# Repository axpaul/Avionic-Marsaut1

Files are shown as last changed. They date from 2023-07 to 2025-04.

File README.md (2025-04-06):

# Avionic-Marsaut1
       
## Marsaut_1 est une fusée expérimentale équipée d'une avionique (électronique de bord) créée par Mines Space. La version n°2 a été lancée au C'space 2022.

> *© 2022 Paul Miailhe, all rights reserved.*  
> *Material licensed under [→ CC BY-NC-SA 4.0](https://creativecommons.org/licenses/by-nc-sa/4.0)*

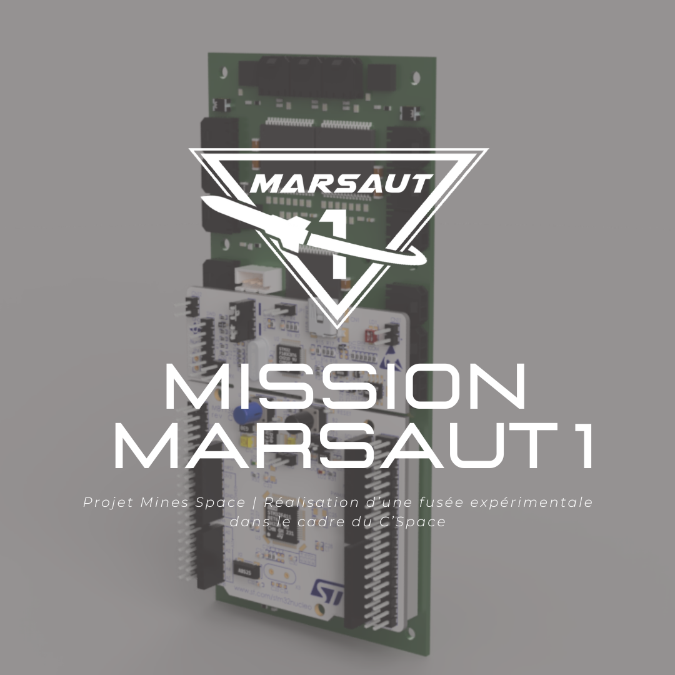
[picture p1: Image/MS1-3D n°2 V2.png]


Grabcad :
- https://grabcad.com/library/avionics-system-for-marsaut-1-rocket-mines-space-1
- https://grabcad.com/library/marsaut-1-fusex-2022-1

La première itération du séquenceur, conçue par Arthur Chassande (plus tard abandonnée), était équipée d'un microcontrôleur Stm32H7. La deuxième version, par Paul Miailhe, utilise directement un Nucléo STM32F411. Ce séquenceur comprenait deux cartes électroniques supplémentaires, une carte d'interface intégrée dans le lanceur, qui abritait l'ensemble des connecteurs, et une carte IHM indépendante concu par Quentin Bakrim, qui pouvait afficher à l'utilisateur l'état actuel de la fusée. Sur la carte mère, on trouve :

## Capteurs de base
- Un assortiment de capteurs de base permettant de collecter les paramètres d'altitude (GPS, IMU, baromètre, température).
- Un "acelerocontact" pour détecter le décollage 

## Enregistrement de données
- Une mémoire flash et une carte SD pour l'enregistrement des données.

## Transmission de données
- Un émetteur de modulation de fréquence à 868 MHZ, fonctionnant en FSK pour la transmission en temps réel des données de vol

## Indicateurs d'état
- Un buzzer et une LED pour indiquer l'état de la carte

## Contrôle des systèmes de déploiement
- Des drivers en pont en H pour contrôler les différents systèmes de déploiement (parachute, drone et nez de cône)

| 3D | Routing  | Description |
|:---:|:---:|:---:|
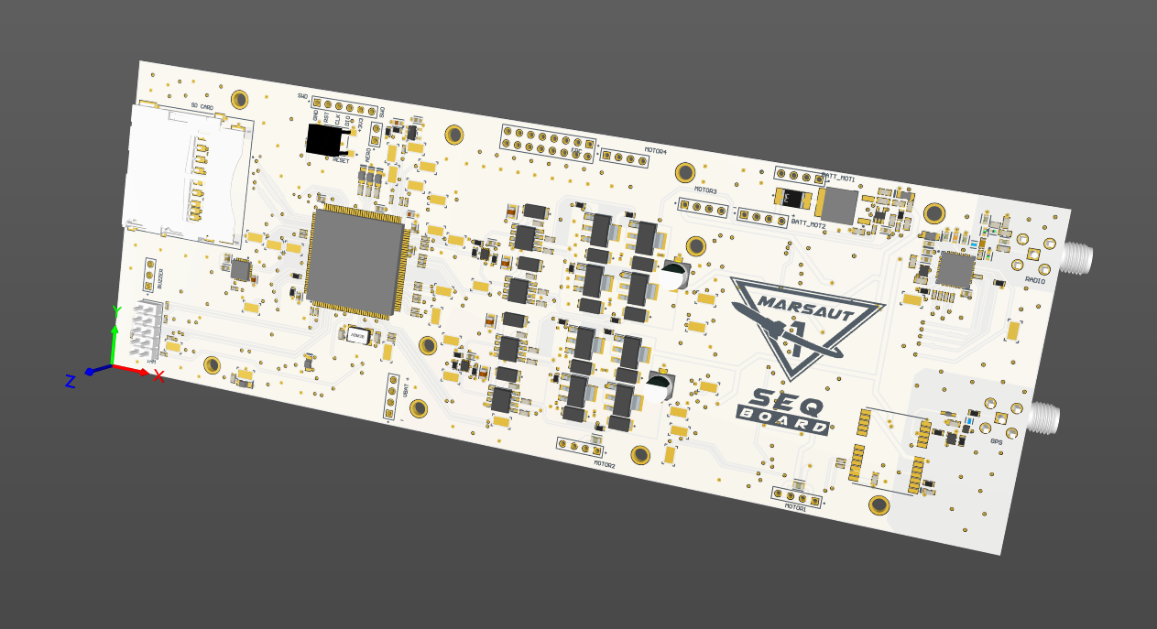
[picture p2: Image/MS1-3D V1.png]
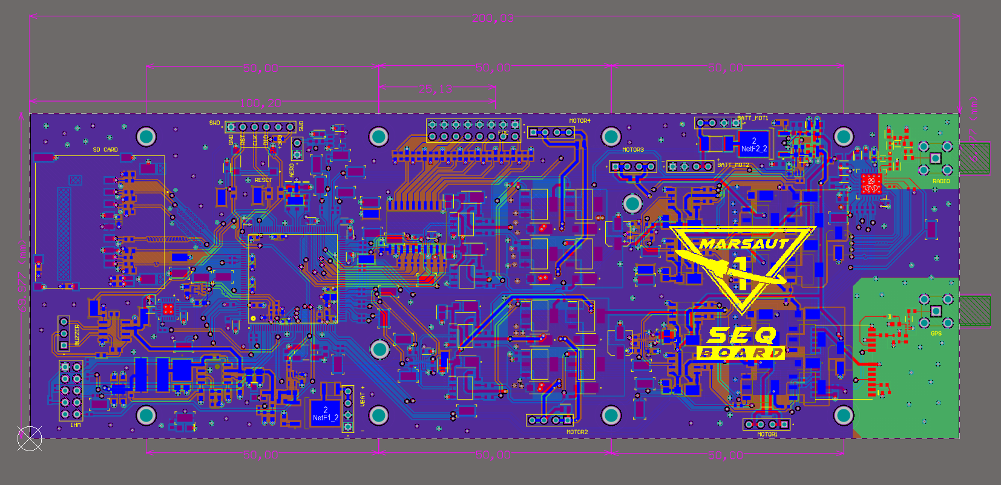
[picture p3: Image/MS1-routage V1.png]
|  |  | V°1 of avionics for Marsaut 1, 6 layers, creator Arthur Chassande |
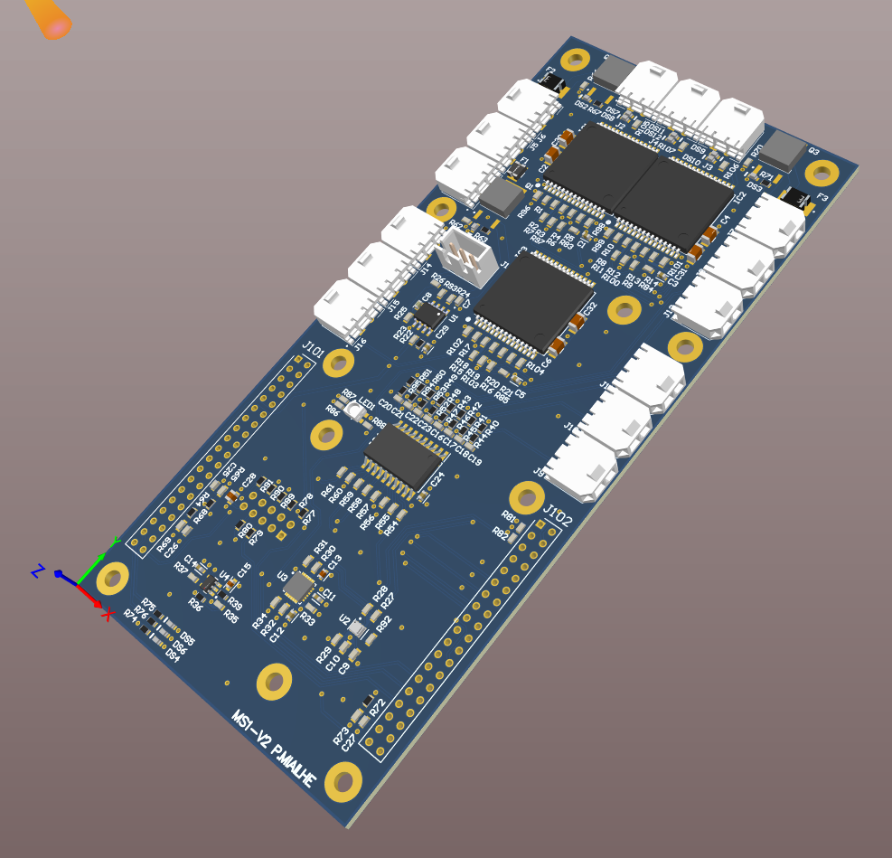
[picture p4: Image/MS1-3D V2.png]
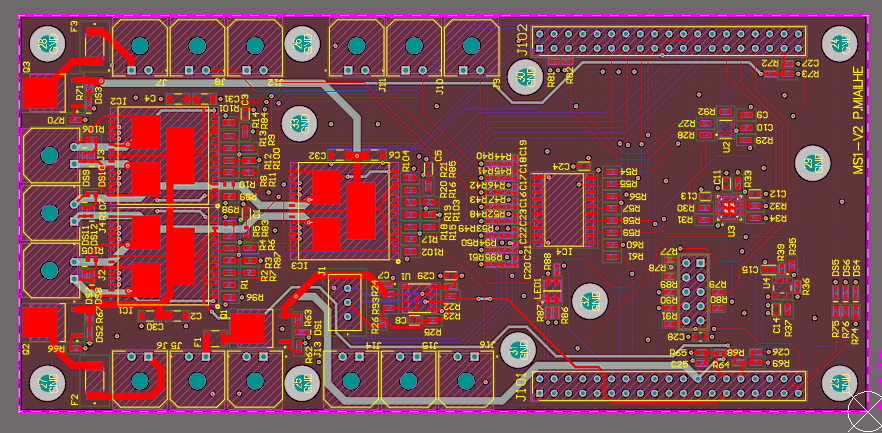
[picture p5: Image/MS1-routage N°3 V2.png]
|  |  | V°2 of avionics for Marsaut 1, 4 layers, fly model, creator Paul Miailhe |
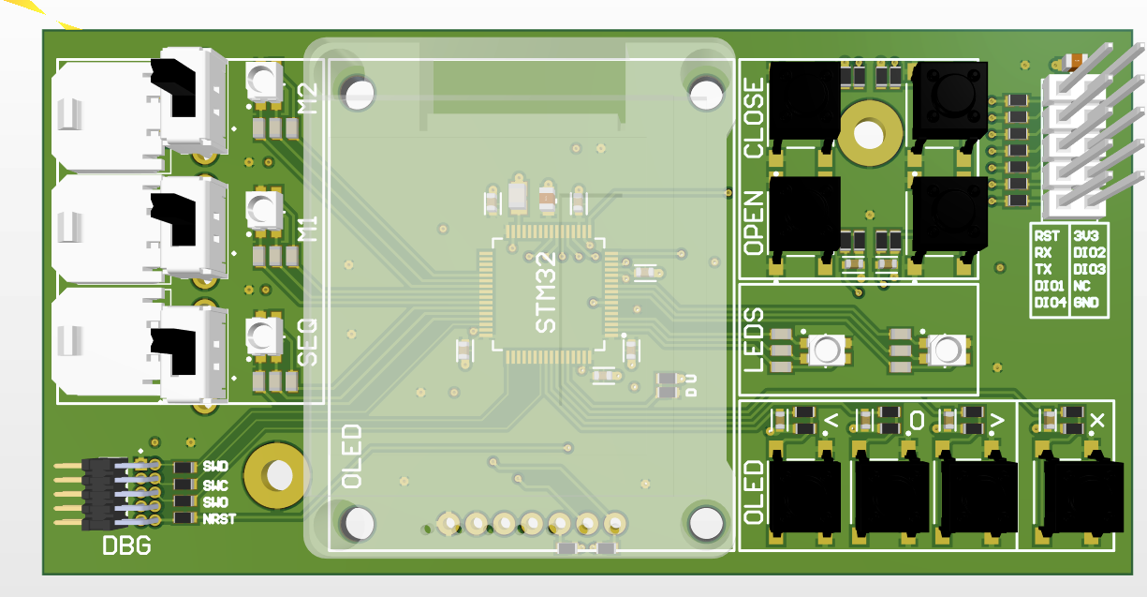
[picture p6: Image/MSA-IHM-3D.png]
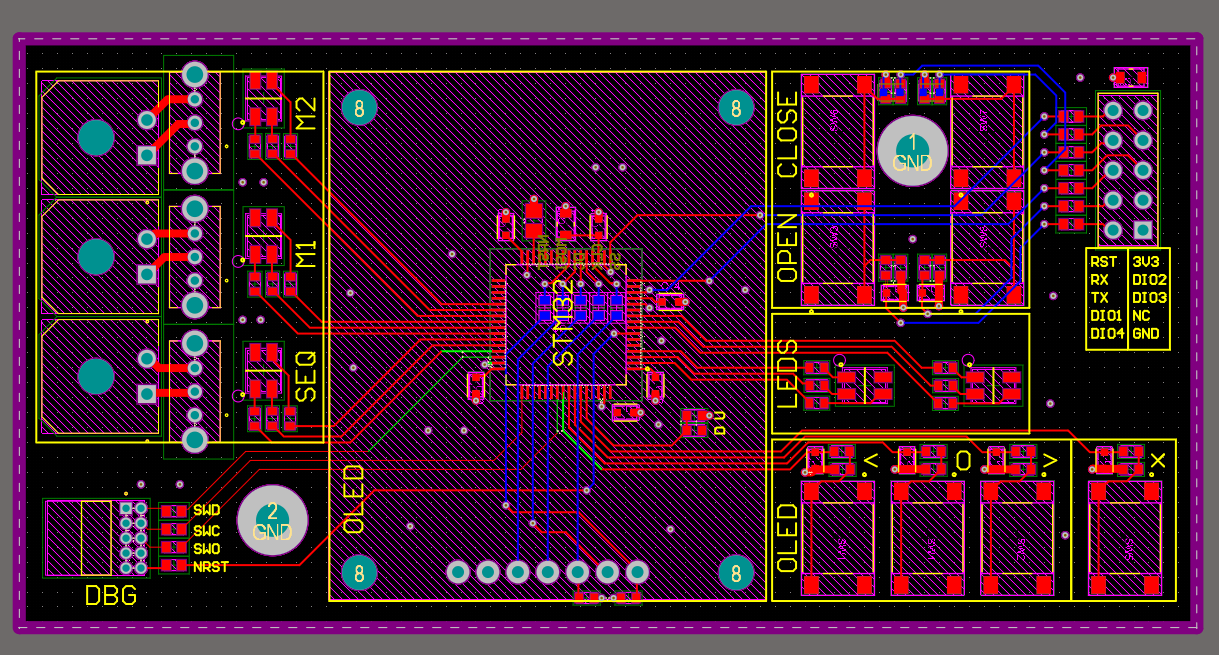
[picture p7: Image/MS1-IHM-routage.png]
|   |   | V°1 of IHM for Marsaut 1, 4 layers, fly model, creator Quentin Bakrim |

## Licence 

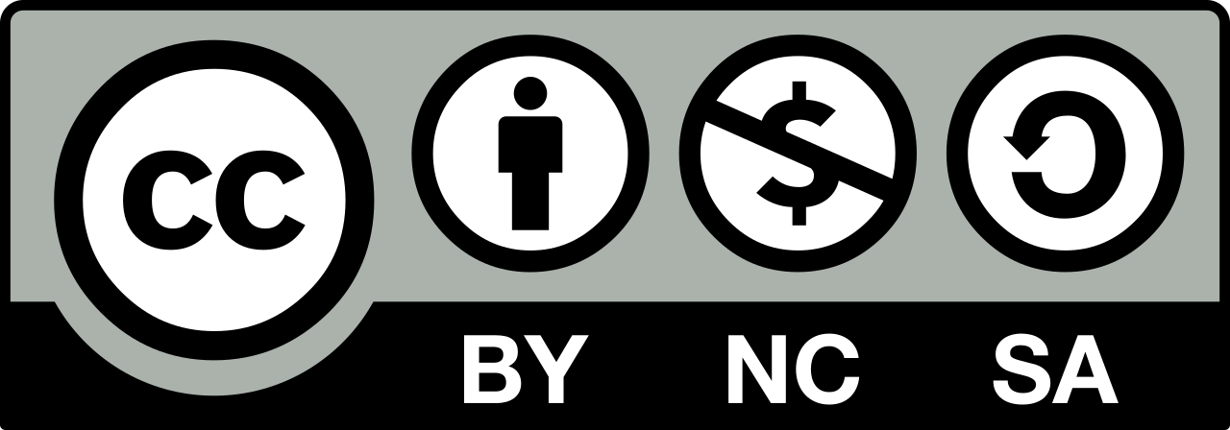
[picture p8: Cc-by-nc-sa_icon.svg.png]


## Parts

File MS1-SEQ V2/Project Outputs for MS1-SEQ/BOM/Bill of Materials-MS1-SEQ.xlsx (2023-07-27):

Comment | Description | Designator | Footprint | LibRef | Quantity
CGA3E2X7R1E104K080AA | Cap Ceramic 100nF 25V X7R 10% Pad SMD 0603 +125°C Automotive T/R | C1, C3, C5, C11, C12, C14, C24, C29 | FP-CGA3E-0_3-0_1-MFG | CMP-08246-002186-1 | 8
GRM31CR71E106KA12L | Chip Multilayer Ceramic Capacitors for General Purpose, 1206, 10uF, X7R, 15%, 10%, 25V | C2, C4, C6, C30, C31, C32 | FP-GRM31C-0_2-e0_3_0_8-MFG | CMP-06035-003589-1 | 6
GRM188R61E105KA12D |  | C7, C16, C17, C18, C19, C20, C21, C22, C23, C25, C26, C27 | CAPC1608X90X35LL10T15 | CMP-2006-02459-1 | 12
C0603C102J3GACTU | CAP CER 1000PF 25V 5% NP0 0603 | C8 | FP-C0603C-CF-MFG | CMP-2006-03010-2 | 1
100nF | Multi-layer Ceramic Capacitor, -55 to 125 degC, 2-Pin SMD (0603), RoHS, Tape and Reel | C9, C10 | SAMS-C0603-2_M | CMP-2000-05332-1 | 2
GRM1885C1H222JA01D | Chip Multilayer Ceramic Capacitors for General Purpose, 0603, 2200pF, C0G, 30ppm/°C, 5%, 50V | C13 | FP-GRM188-0_1-e0_2_0_5-MFG | CMP-06035-056041-1 | 1
C1608X7R1H334K080AC | Multilayer Ceramic Capacitors 330nF ±10% 50V X7R SMD 0603 | C15 | FP-C1608-080-0_1-IPC_B | CMP-2000-07551-2 | 1
C2012X6S1C106K125AC | Multilayer Ceramic Capacitors 10μF ±10% 16V X6S SMD 0805 | C28 | FP-C2012-125-0_2-MFG | CMP-08246-003655-1 | 1
HSMG-C190 | Chip LED, Green, 2.2 V, -40 to 85 degC, 2-Pin SMD, RoHS, Tape and Reel | DS1, DS2, DS3, DS7, DS9, DS11 | AVAG-HSMX-C190_V | CMP-1744-00002-1 | 6
HSMY-C190 | LED Uni-Color Yellow, 65 mW, 20 mA, -40 to 85 degC, 2-Pin SMD, RoHS, Tape and Reel | DS4, DS5, DS6 | AVAG-HSMX-C190_V | CMP-1744-00003-1 | 3
HSMH-C190 | LED Uni-Color Red, 65 mW, 20 mA, -40 to 85 degC, 2-Pin SMD, RoHS, Tape and Reel | DS8, DS10, DS12 | AVAG-HSMX-C190_V | CMP-1744-00004-1 | 3
1210L110/16WR | PTC RESET FUSE 16V 1.1A 1210 | F1 | FP-1210L110-16WR-MFG | CMP-08606-000029-1 | 1
1812L260_16MR | Resettable Fuse | F2, F3 | 1812L010DR | 1812L260_16MR | 2
VNH5019ATR-E | Integrated Circuit | IC1, IC2, IC3 | VNH5019A-E_1 | VNH5019ATR-E | 3
74HC7540D,112 | Integrated Circuit | IC4 | SOIC127P1032X265-20N | 74HC7540D,112 | 1
B3B-XH-A_LF | Connector | J1 | B3BXHALFSN | B3B-XH-A_LF__SN_ | 1
436500200 |  | J2, J3, J4, J5, J6, J7, J8, J9, J10, J11, J12, J13, J14, J15, J16 | MOLEX_436500200 | 436500200 | 15
BCS-119-L-D-TE-031 | Connector | J101, J102 | RHDR38W51P254_2X19_4826X508X737P | BCS-119-L-D-TE-031 | 2
150141M173100 | SMD Full-Color Top LED, WL-SFTW, Red & Green & Blue | LED1 | 3528_A | CMP-1431-00001-1 | 1
TSW-105-15-G-D | 0.025" SQ Post Header, Through-hole, Vertical, -55 to 125 degC, 2.54 mm Pitch, 10-Pin, Male, RoHS | P10 | SMTC-TSW-105-15-X-D | CMP-1024-00369-1 | 1
FDD4243 | OptiMOS-P2 Power-Transistor, -40 V VDS, -85 A ID, PG-TO252-3-313, Reel, Green | Q1, Q2, Q3 | INF-PG-TO252-3-313_L | CMP-1138-00157-1 | 3
0R | Chip Resistor, 0 Ohm, +/- 5%, 0.1 W, -55 to 155 degC, 0603 (1608 Metric), RoHS, Tape and Reel | R1, R2, R3, R4, R5, R10, R11, R12, R13, R14, R17, R18, R19, R20, R21, R23, R24, R27, R28, R29, R30, R31, R32, R33, R34, R35, R37, R54, R55, R56, R57, R58, R59, R60, R61, R83, R84, R85, R92, R93 | RESC1608X55X25ML10T15 | CMP-2100-03667-1 | 40
3K3 | Chip Resistor, 3.3 KOhm, +/- 1%, 0.1 W, -55 to 155 degC, 0603 (1608 Metric), RoHS, Tape and Reel | R6, R7, R8, R9, R15, R16 | RESC1608X55X25ML10T15 | CMP-1012-00567-2 | 6
ERJ3EKF1002V | Chip Resistor, 10 KOhm, +/- 1%, 0.1 W, -55 to 155 degC, 0603 (1608 Metric), RoHS, Tape and Reel | R22, R36, R39, R40, R41, R42, R43, R44, R45, R46, R47, R48, R49, R50, R51, R52, R53, R64, R68, R72, R94, R95 | RESC1609X55X30LL15T15 | CMP-1012-00623-3 | 22
ERJ-3GEYJ155V |  | R25 | RESC1608X55X30ML15T15 | CMP-2000-00727-1 | 1
ERJ-3EKF1503V |  | R26 | RESC1608X55X30NL15T15 | CMP-1012-00754-2 | 1
RC0603JR-070RL | Chip Resistor, 0 Ohm, +/- 5%, 0.1 W, -55 to 155 degC, 0603 (1608 Metric), RoHS, Tape and Reel | R62, R66, R70 | RESC1608X55X25ML10T15 | CMP-2100-03667-1 | 3
ERJ-3EKF2001V |  | R65, R69, R73 | RESC1608X55X30ML15T15 | CMP-2000-00317-1 | 3
CRCW06030000Z0EA | Chip Resistor, 0 Ohm, Jumper, 100 mW, -55 to 155 degC, 0603 (1608 Metric), RoHS, Tape and Reel | R77, R78, R79, R80, R89, R90, R91 | RESC1609X50X30NL8T20 | CMP-2000-03816-5 | 7
RC0603FR-074K7L | Chip Resistor, 4.7 KOhm, +/- 1%, 0.1 W, -55 to 155 degC, 0603 (1608 Metric), RoHS, Tape and Reel | R81, R82 | RESC1608X55X25LL10T15 | CMP-2000-06942-1 | 2
ERJ-3EKF1000V |  | R86, R87, R88 | RESC1608X55X30LL15T15 | CMP-2000-00179-1 | 3
ERA3AEB104V |  | R96, R97, R98, R99, R100, R101, R102, R103, R104 | RESC1608X55X30ML20T20 | CMP-2000-00875-1 | 9
ERA-3AEB751V |  | R105, R106, R107 | RESC1608X55X30ML20T20 | CMP-2000-00122-1 | 3
RE46C100S8F |  | U1 | SOIC127P600X175-8N | RE46C100S8F | 1
BMP280 | SENSOR PRESSURE ABS | U2 | FP-BMP280-MFG | CMP-2000-05076-3 | 1
MPU-6050 | 3-Axis Gyroscope, Accelerometer and a Digital Motion Processor(TM) (DMP), 2.375 to 3.46 V, -40 to 85 degC, 24-Pin QFN, RoHS, Tape and Reel | U3 | IS-QFN-24_V | CMP-1753-00002-2 | 1
SN74LVC1G17DBVT | IC BUF NON-INVERT 5.5V SOT23-5 | U4 | FP-DBV0005A-MFG | CMP-0859-00041-5 | 1

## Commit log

2023-07-27 add altium files
    [1EDN7550BXTSA1.PcbLib, 1EDN7550BXTSA1.SchLib, BCS-119-L-D-TE.PcbLib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]
2023-07-28 add files IHM
    [43650-0200.PcbLib, 43650-0200.SchLib, 436500200.PcbLib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]

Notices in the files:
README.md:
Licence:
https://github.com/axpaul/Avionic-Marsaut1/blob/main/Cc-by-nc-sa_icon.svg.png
